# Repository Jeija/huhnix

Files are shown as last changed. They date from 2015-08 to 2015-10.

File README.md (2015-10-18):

# Huhnix
Huhnix is software for an automatic slider door, such as a door for a hen house (hence the name). The slider door opens automatically every morning at a set time and is operated with two buttons or via WiFi. Settings can be adjusted with WiFi device that can access the settings webpage. Huhnix uses two microprocessors that communicate over a UART interface.

## Pictures
Slider with electronics
Configuration site on smartphone
Henhouse with slider and buttons
...and a chicken

## Documentation
### Main controller: AVR
The main processor receives inputs from two buttons that are used to make the doors slide up or down and keeps all the settings and keeps track of the time (so no need for a RTC).

### Secondary controller: ESP8266
The ESP8266 provides a configuration interface by acting as an access point that mobile devices can connect to in order to access a simple web interface. This web interface can be used to access system information such as the system clock and battery levels. The ESP8266 (e.g. within an ESP-01 module) is only active, when the main processor wakes it up. That is the case, when any of the slider control buttons have been pressed. This is crucial to save limited battery power. The battery can be charged using a solar panel. The ESP8266 software is based on the IoT SDK version 1.4 from Espressif.

### Controller communication protocol
#### Definitions
Due to restrictions of the ESP-01 module, the two processors have to communicate over the serial port. The protocol is as follows:
* Baudrate 9600 Baud, no parity, 8 bits, no stopbit, no flow control
* Each processor must always listen for commands and can always send commands. When a processor receives a command, it must answer immediately or perform the requested action and may not execute another command at the same time.
* If any unknown or unexpected string / command / ... is received by any processor, it has to be ignored. This is due to the fact that the ESP8266 SDK ROM outputs debug information, which cannot be disabled.
* Each command is terminated by "\r\n". The command itself may not contain any of these characters.

#### Commands
| ESP8266 command	| Description	|
|---	|---	|
| time	| For debugging only, outputs human-readable DCF77 time information	|
| dcf	| For debugging only, outputs debugging data on the DCF77 signal	|
| time_get	| To be used by the AVR controller. Outputs time data in a machine (and also human) readable form: Seconds, minutes, hours, date (of month), month, year (only last two digits) and day (of week) are transferred in this order as human-readable strings with a space in between each value. If no valid time value is available, the ESP8266 answers with the character x.	|

| AVR command	| Description	|
|---	|---	|
| slider_down	| Move the slider door down. Must be acknowledged by sending the string "sld_ok".	|
| slider_up	| Move the slider door up. Must be acknowledged by sending the string "slu_ok".	|
| systime_get	| Gets the current system time in the same format as time_get (for debugging and for Display on the web frontend).	|
| battery_get	| To be used by the ESP8266. Voltage and percent values are transferred as two human-readable numbers with a space in between them. The voltage value is transferred as an unsigned integer with the value being measured in 100mV (so a value of 123 indicates 12,3V). The percentage value is an estimated integer number between 0 and 100.	|
| opentime_get	| Get time at which to open the slider automatically (time of day). Hours and minutes are transferred as two human-readable integer numbers with a space in between them. An hour value of 25 indicates that the slider is not supposed to be opened at all.	|
| opentime_set <hours> <minutes>	| Tell AVR to open the slider at <hours>:<minutes> each day, where hours and minutes are integers seperate by a space. Must be acknowledged by sending the string "ots_ok"	|

### AVR hardware
The ATMega128A's fusebits are `E:FF, H:89, L:FF`, make sure to disable ATMega 103 compatibility mode! I use a cheap [chinese ATMega128A development board from LC Studio](http://www.lctech-inc.com/Hardware/Detail.aspx?id=68611f14-46cd-4676-95df-f1246689dbba) with the power LED desoldered in order to save power. A custom addon board (PCB design files in `hardware` directory, currently only tested with a prototype board) is stacked on top of the pin headers of the development board. This addon board has connectors for the DCF77 real time clock (I use the one from [conrad.de](http://www.conrad.de/ce/de/product/641138), for buttons, for 12V power sensing, the 5V power supply (provided by a step down converter from a lead-acid battery) and for a 2-channel relay board (HL-52 V 1.0).

## Attribution / License
The PCB design and schematic uses [Jerry Dunmire's ESP8266 KiCAD library](https://github.com/jdunmire/kicad-ESP8266) in the `hardware/libraries/ESP8266` directory, licensed under CC BY-SA 4.0. I license my hardware designs under the [CC BY-SA 4.0 license](https://creativecommons.org/licenses/by-sa/4.0/).

The ESP8266 software uses [Spritetm's libesphttpd with espfs](https://github.com/Spritetm/libesphttpd) in `esp8266/libesphttpd`. All my code is licensed under the [MIT license](http://opensource.org/licenses/MIT).

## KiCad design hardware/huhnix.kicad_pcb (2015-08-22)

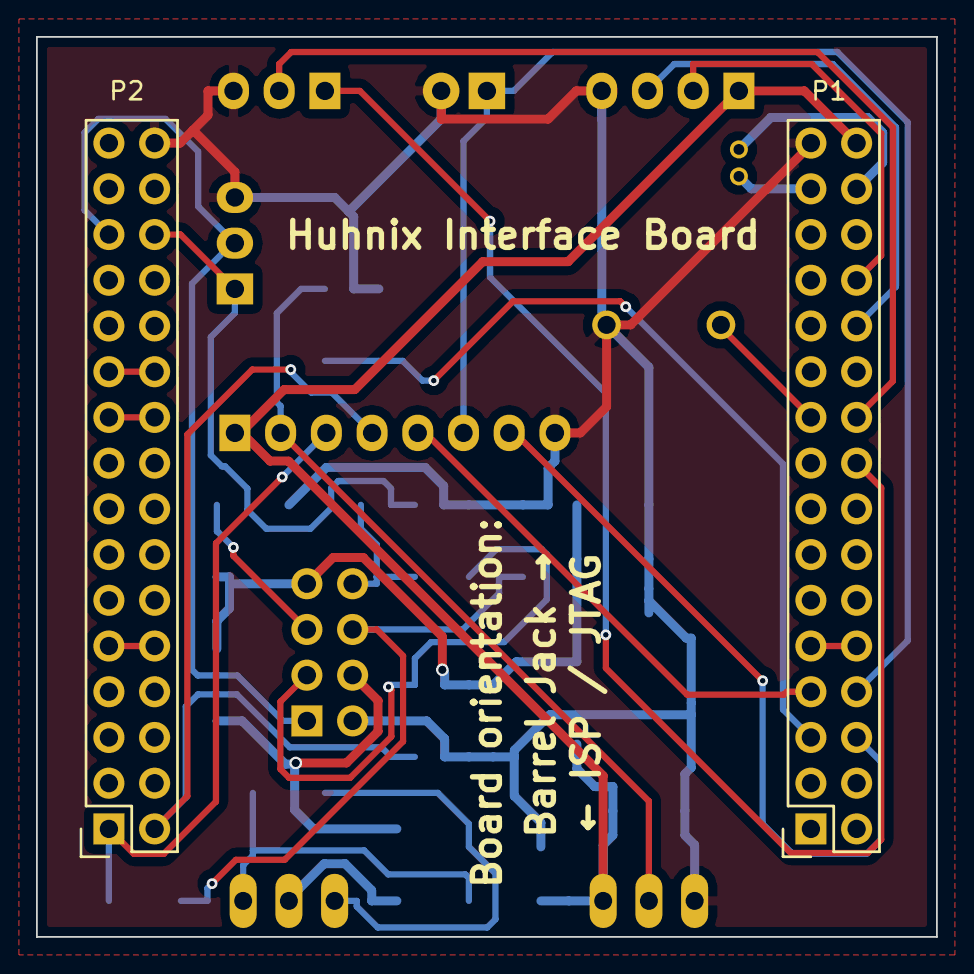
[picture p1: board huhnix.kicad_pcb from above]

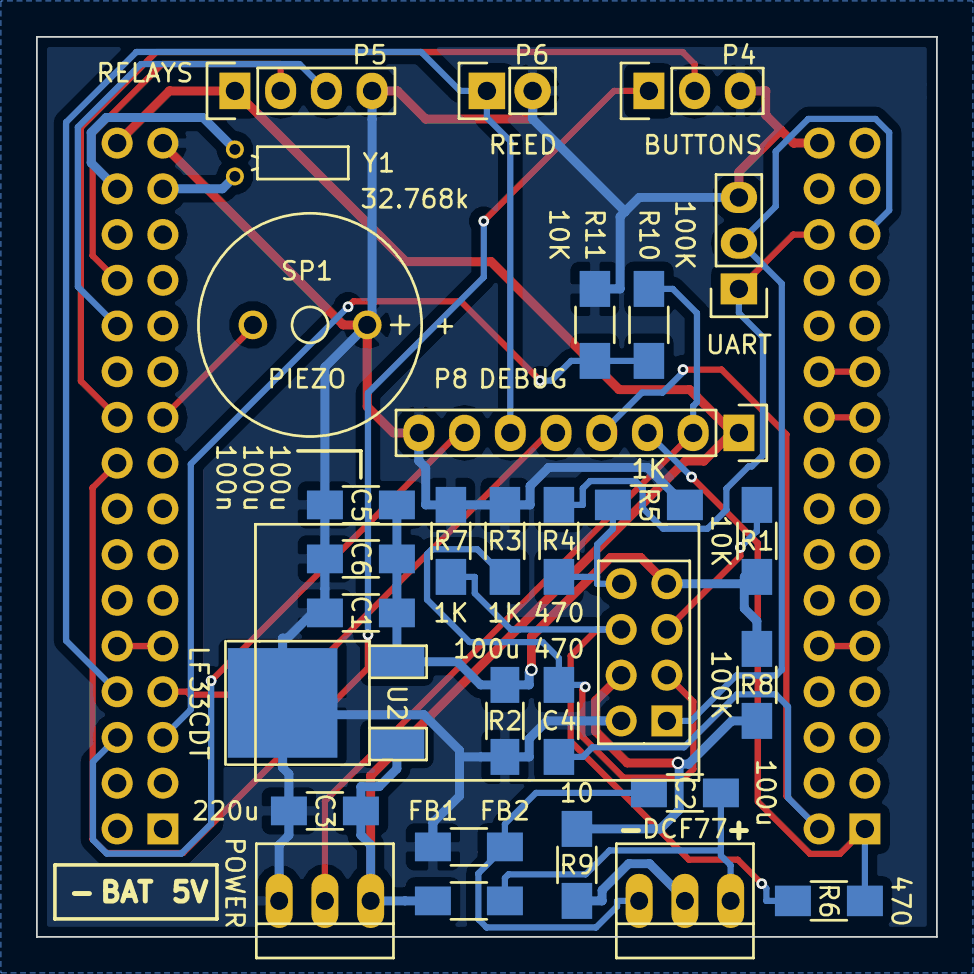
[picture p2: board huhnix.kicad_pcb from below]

Board: 2 copper layers, 50.0 x 50.0 mm, 32 parts (30 on the bottom side), 31 nets.

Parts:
C1: 100n; C_1206_HandSoldering
C2, C4, C5, C6: 100u; C_1206_HandSoldering
C3: 220u; C_1206_HandSoldering
FB1, FB2: FILTER; C_1206_HandSoldering
P1, P2: CONN_02X16; Socket_Strip_Straight_2x16
P3: DCF77; PINHEAD1-3
P4: BUTTONS; Pin_Header_Straight_1x03
P5: RELAYS; Pin_Header_Straight_1x04
P6: REED; Pin_Header_Straight_1x02
P7: POWER; PINHEAD1-3
P8: UART; Pin_Header_Straight_1x03
P9: DEBUG; Pin_Header_Straight_1x08
R1, R11: 10K; R_1206_HandSoldering
R2, R4, R6: 470; R_1206_HandSoldering
R3, R5, R7: 1K; R_1206_HandSoldering
R8, R10: 100K; R_1206_HandSoldering
R9: 10; R_1206_HandSoldering
SP1: PIEZO; MagneticBuzzer_ProSignal_ABT-410-RC
U1: ESP-01v090; ESP-01
U2: LF33CDT; TO-252-2Lead
Y1: 32.768k; Crystal_Round_Horizontal_2mm

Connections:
+3V3: C1.1, C4.1, C5.1, C6.1, R1.1, R8.1, U1.7, U2.3
+5V: C3.1, FB1.1, P1.32, P5.1, P7.1, P9.1, U2.1
+BATT: P7.2, P9.2, R10.1
/Aref: P1.9, P1.10
/PB2: P1.24, P5.3
/PB4: P1.26, P5.2
/PE4: P1.18, P4.1
/PE6: P1.20, P4.2
/PE7: P1.19, SP1.1
/PF0: P1.7, P9.5
/PF1: P1.8, P6.1, P9.6
/PF2: P1.5, R10.2, R11.1
/PF3: P1.6, P9.7
/PG0: P2.21, P2.22
/PG1: P2.19, P2.20
/PG2: P2.9, P2.10
/PG3: P1.30, Y1.1
/PG4: P1.29, Y1.2
DCF: P3.2, R9.2
ESP_EN: P2.2, P9.4, R2.1
ESP_PRGM: P2.1, P9.3, R6.1
GND: C1.2, C3.2, C4.2, C5.2, C6.2, FB2.1, P1.31, P2.32, P4.3, P5.4, P6.2, P7.3, P8.3, P9.8, R3.2, R5.2, R7.2, R11.2, SP1.2, U1.2, U2.2
unnamed: C2.1, FB1.2, P3.1
unnamed: C2.2, FB2.2, P3.3
unnamed: R1.2, U1.5
unnamed: R2.2, R3.1, U1.3
unnamed: R4.2, R5.1, U1.8
unnamed: R6.2, R7.1, U1.6
unnamed: R8.2, R9.1, U1.4
RXD: P2.27, P8.2, U1.1
TXD: P2.28, P8.1, R4.1

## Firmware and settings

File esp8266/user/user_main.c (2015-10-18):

// System
#include "ets_sys.h"
#include "osapi.h"
#include "gpio.h"
#include "os_type.h"
#include "user_interface.h"

// HTTPD
#include "webpages-espfs.h"
#include "httpdespfs.h"
#include "httpd.h"

// Configuration
#include "user_config.h"

bool time_valid = false;
struct TimeSpec {
	uint8_t seconds;
	uint8_t minutes;
	uint8_t hours;
	uint8_t date;
	uint8_t month;
	uint8_t year;
	uint8_t dow;
} time;

bool dcf_decoder_readjust = false;

os_timer_t dcf_read_timer;
os_timer_t dcf_decode_timer;
os_timer_t time_inc_timer;

#define ANS_BUF_SIZE 30
uint8_t ans_buf_iter = 0;
char ans_buf[ANS_BUF_SIZE];

#define CMD_BUF_SIZE 16
uint8_t cmd_buf_iter = 0;
char cmd_buf[CMD_BUF_SIZE];

uint8_t dcf_hc = 0;
uint8_t dcf_lc = 0;

uint8_t signal[60];
uint8_t signal_iter = 0;

#define user_procTaskPrio 0
#define user_procTaskQueueLen 1
os_event_t user_procTaskQueue[user_procTaskQueueLen];

// Returns FALSE if value is invalid
uint8_t decode_value(uint8_t firstbit, uint8_t lastbit) {
	++firstbit; ++lastbit;
	uint8_t bitnum = lastbit - firstbit;
	uint8_t value = 0;

	// No need for math.h's pow() this way
	if (signal[firstbit]) value += 1;
	if (bitnum >= 1 && signal[firstbit + 1]) value += 2;
	if (bitnum >= 2 && signal[firstbit + 2]) value += 4;
	if (bitnum >= 3 && signal[firstbit + 3]) value += 8;

	// BCD notation
	if (bitnum >= 4 && signal[firstbit + 4]) value += 10;
	if (bitnum >= 5 && signal[firstbit + 5]) value += 20;
	if (bitnum >= 6 && signal[firstbit + 6]) value += 40;
	if (bitnum >= 7 && signal[firstbit + 7]) value += 80;

	return value;
}

bool check_parity(uint8_t firstbit, uint8_t lastbit, uint8_t paritybit) {
	++firstbit; ++lastbit; ++paritybit;
	uint8_t i;
	uint8_t parity = 0;
	for (i = firstbit; i <= lastbit; i++)
		parity ^= signal[i];

	return (parity == signal[paritybit]);
}

void dcf2time(void) {
	if (signal_iter == 60) {
		time.seconds = 0;

		// Assume time signal is good only if all parities are correct
		if (check_parity(21, 27, 28) && check_parity(29, 34, 35) && check_parity(36, 57, 58)) {
			time.minutes = decode_value(21, 27);
			time.hours = decode_value(29, 34);
			time.date = decode_value(36, 41);
			time.dow = decode_value(42, 44);
			time.month = decode_value(45, 49);
			time.year = decode_value(50, 57);

			time_valid = true;
		}
	}
}

/*** Timers ***/
void dcf_decode_timer_cb(void) {
	// Last second of minute, no time signal, readjust
	if (dcf_hc <= 10) {
		dcf2time();
		signal_iter = 0;
		os_timer_disarm(&dcf_decode_timer);
		dcf_decoder_readjust = true;
	}

	if (signal_iter < 60) signal[signal_iter++] = (dcf_hc > 35);
	dcf_lc = 0;
	dcf_hc = 0;
}

void dcf_decode_timer_adjust(void) {
	os_timer_disarm(&dcf_decode_timer);
	os_timer_setfn(&dcf_decode_timer, (os_timer_func_t *) dcf_decode_timer_cb, NULL);
	os_timer_arm(&dcf_decode_timer, 1000, 1);
}

void dcf_read_timer_cb(void)
{
	// Inverted signal, add to low count (lc) when pin is true
	if (GPIO_INPUT_GET(2)) {
		dcf_lc++;
		if (dcf_decoder_readjust) {
			dcf_decode_timer_adjust();
			dcf_decoder_readjust = false;
		}
	} else
		dcf_hc++;
}

void time_inc_timer_cb(void) {
	time.seconds++;
	if (time.seconds == 60) {
		time.seconds = 0;
		time.minutes++;
		if (time.minutes == 60) {
			time.minutes = 0;
			time.hours++;
			if (time.hours == 24) {
				time.hours = 0;
				time.date++;
				time.dow++;
				// Ignore the rest, receive that from DCF77
			}
		}
	}
}

void ap_init(void) {
	// Check if configuration is ok already (compare SSID)
	struct softap_config netcfg;

	wifi_softap_get_config(&netcfg);
	if (os_strcmp(WIFI_SSID, netcfg.ssid) == 0) return;

	// Configuration is not good, change config and reboot
	system_restore();
	os_memcpy(netcfg.ssid, WIFI_SSID, os_strlen(WIFI_SSID));
	netcfg.ssid[os_strlen(WIFI_SSID)] = 0x00;
	netcfg.ssid_len = os_strlen(WIFI_SSID);
	netcfg.channel = 1;
	netcfg.authmode = AUTH_OPEN;
	netcfg.beacon_interval = 100;

	wifi_softap_set_config(&netcfg);
	wifi_set_opmode(0x02);
	system_restart();
}

/*** Loop ***/
static void ICACHE_FLASH_ATTR loop(os_event_t *events) {
	char c;
	int res = uart_rx_one_char(&c);

	if(res != 1) {
		if (c != '\r' && c != '\n') {
			if (cmd_buf_iter + 1 < CMD_BUF_SIZE)
				cmd_buf[cmd_buf_iter++] = c;
		} else {
			cmd_buf[cmd_buf_iter] = 0x00;
			cmd_buf_iter = 0;
			if (os_strcmp(cmd_buf, "time") == 0) {
				if (time_valid) {
					os_printf("Zeit: %d.%d.%d, %d:%d:%d, DOW %d\r\n", time.date, time.month, time.year, time.hours, time.minutes, time.seconds, time.dow);
				} else {
					os_printf("No valid time information yet!\r\n");
				}
			} else if (os_strcmp(cmd_buf, "dcf") == 0) {
				os_printf("DCF77 status information:\r\n");
				os_printf("Received bits this minute: %d\r\n", signal_iter);
				os_printf("High count %d, Low count %d, Total %d\r\n", dcf_hc, dcf_lc, dcf_hc + dcf_lc);
				os_printf("Signal buffer:\r\n");
				uint8_t i;
				for (i = 0; i < 60; i++) os_printf("%d", signal[i]);
				os_printf("\r\n");
			} else if (os_strcmp(cmd_buf, "time_get") == 0) {
				if (time_valid) {
					os_printf("%d %d %d %d %d %d %d\r\n", time.seconds, time.minutes, time.hours, time.date, time.month, time.year, time.dow);
				} else {
					os_printf("x\r\n");
				}
			} else if (os_strcmp(cmd_buf, "hello") == 0) {
				os_printf("hel_ok\r\n");
			}
		}
	}
	system_os_post(user_procTaskPrio, 0, 0);
}

/**
 * get_answer
 * Writes answer in global ans_buf variable
 * Ignores answers that are longer than ANS_BUF_SIZE
 * Returns false if no answer was received, otherwise true
 *
 * ms_to_answer maximum 1000ms due to watchdog!
 */
bool get_answer(uint16_t ms_to_answer) {
	ans_buf_iter = 0;
	uint16_t time_ms = 0;

	while (time_ms <= ms_to_answer) {
		char c;
		int res = uart_rx_one_char(&c);

		if (res == 1) {
			os_delay_us(1000);
			time_ms++;
		} else {
			if (c != '\r' && c != '\n') {
				if (ans_buf_iter + 1 < ANS_BUF_SIZE)
					ans_buf[ans_buf_iter++] = c;
			} else {
				ans_buf[ans_buf_iter] = 0x00;
				return true;
			}
		}
	}

	return false;
}

/**
 * Returns the nth integer from a string in which integers are separated by spaces
 * The integer must be an unsigned 8-bit integer, the string must be null-terminated
 * Returns 255 on error (nth too high), but string must contain valid integers
 */
uint8_t integer_from_string(char *buf, uint8_t nth) {
	char numberbuf[4];
	uint8_t numberbuf_iter = 0;
	uint8_t i = 0;
	uint8_t intnum = 0;
	while (buf[i] != 0x00) {
		if (buf[i] == ' ') {
			intnum++;
			if (intnum > nth) break;
		} else if (intnum == nth) {
			numberbuf[numberbuf_iter++] = buf[i];
		}

		i++;
	}

	if (intnum < nth) return 255;

	numberbuf[numberbuf_iter] = 0x00;
	return (uint8_t) atoi(numberbuf);
}

/**
 * HTTP commands
 * They forward the corresponding command to the AVR controller and decode the
 * answer. The may then forward that answer to the HTTP client in a human-readable
 * format.
 */
int cmd_slider_up(HttpdConnData *conn) {
	uint8_t i;
	for (i = 0; i < 4; i++) {
		os_printf("\r\nslider_up\r\n");
		bool res = get_answer(200);
		if (res == true && os_strcmp("slu_ok", ans_buf) == 0) {
			os_printf("Leaving with success state\r\n");
			httpdSend(conn, "ok", -1);
			return HTTPD_CGI_DONE;
		}
	}

	os_printf("Leaving with error state, buffer is %s\r\n", ans_buf);
	httpdSend(conn, "Keine Antwort vom AVR-Controller", -1);
	return HTTPD_CGI_DONE;
}

int cmd_slider_down(HttpdConnData *conn) {
	uint8_t i;
	for (i = 0; i < 4; i++) {
		os_printf("\r\nslider_down\r\n");
		bool res = get_answer(200);
		if (res == true && os_strcmp("sld_ok", ans_buf) == 0) {
			httpdSend(conn, "ok", -1);
			return HTTPD_CGI_DONE;
		}
	}

	httpdSend(conn, "Keine Antwort vom AVR-Controller", -1);
	return HTTPD_CGI_DONE;
}

int cmd_opentime_get(HttpdConnData *conn) {
	uint8_t i;
	for (i = 0; i < 4; i++) {
		os_printf("\r\nopentime_get\r\n");
		bool res = get_answer(200);
		if (res == true) {
			uint8_t hours = integer_from_string(ans_buf, 0);
			uint8_t minutes = integer_from_string(ans_buf, 1);

			char resbuf[50];
			if (hours == 25)
				os_sprintf(resbuf, "Klappe wird nicht automatisch geöffnet");
			else
				os_sprintf(resbuf, "Aufmachzeit ist %d:%d Uhr", hours, minutes);
			httpdSend(conn, resbuf, -1);
			return HTTPD_CGI_DONE;
		}
	}

	httpdSend(conn, "Keine Antwort vom AVR-Controller", -1);
	return HTTPD_CGI_DONE;
}

int cmd_systime_get(HttpdConnData *conn) {
	uint8_t i;
	for (i = 0; i < 4; i++) {
		os_printf("\r\nsystime_get\r\n");
		bool res = get_answer(200);
		if (res == true) {
			uint8_t seconds = integer_from_string(ans_buf, 0);
			uint8_t minutes = integer_from_string(ans_buf, 1);
			uint8_t hours = integer_from_string(ans_buf, 2);
			uint8_t date = integer_from_string(ans_buf, 3);
			uint8_t month = integer_from_string(ans_buf, 4);
			uint8_t year = integer_from_string(ans_buf, 5);
			uint8_t dow = integer_from_string(ans_buf, 6);

			char dow_readable[30];
			if (dow == 255) continue;
			else if (dow == 1) os_strcpy(dow_readable, "Montag");
			else if (dow == 2) os_strcpy(dow_readable, "Dienstag");
			else if (dow == 3) os_strcpy(dow_readable, "Mittwoch");
			else if (dow == 4) os_strcpy(dow_readable, "Donnerstag");
			else if (dow == 5) os_strcpy(dow_readable, "Freitag");
			else if (dow == 6) os_strcpy(dow_readable, "Samstag");
			else if (dow == 7) os_strcpy(dow_readable, "Sonntag");
			else if (dow == 0) os_strcpy(dow_readable, "Ungültige Systemzeit");

			char resbuf[80];
			os_sprintf(resbuf, "%s, %d.%d.%d %d:%d:%d Uhr", dow_readable, date, month, year, hours, minutes, seconds);
			httpdSend(conn, resbuf, -1);
			return HTTPD_CGI_DONE;
		}
	}

	httpdSend(conn, "Keine Antwort vom AVR-Controller", -1);
	return HTTPD_CGI_DONE;
}

int cmd_systime_set(HttpdConnData *conn) {
	// Parse command from GET parameters
	char seconds_str[3];
	char minutes_str[3];
	char hours_str[3];
	char date_str[3];
	char month_str[3];
	char year_str[3];
	char dow_str[2];

	httpdFindArg(conn->getArgs, "seconds", seconds_str, sizeof(seconds_str));
	httpdFindArg(conn->getArgs, "minutes", minutes_str, sizeof(minutes_str));
	httpdFindArg(conn->getArgs, "hours", hours_str, sizeof(hours_str));
	httpdFindArg(conn->getArgs, "date", date_str, sizeof(date_str));
	httpdFindArg(conn->getArgs, "month", month_str, sizeof(month_str));
	httpdFindArg(conn->getArgs, "year", year_str, sizeof(year_str));
	httpdFindArg(conn->getArgs, "dow", dow_str, sizeof(dow_str));

	time.seconds = atoi(seconds_str);
	time.minutes = atoi(minutes_str);
	time.hours = atoi(hours_str);
	time.date = atoi(date_str);
	time.month = atoi(month_str);
	time.year = atoi(year_str);
	time.dow = atoi(dow_str);
	time_valid = true;

	httpdSend(conn, "ok", -1);
	return HTTPD_CGI_DONE;
}

int cmd_battery_get(HttpdConnData *conn) {
	uint8_t i;
	for (i = 0; i < 4; i++) {
		os_printf("\r\nbattery_get\r\n");
		bool res = get_answer(200);
		if (res == true) {
			uint8_t voltage = integer_from_string(ans_buf, 0);
			uint8_t percent = integer_from_string(ans_buf, 1);

			char resbuf[50];
			os_sprintf(resbuf, "Batteriespannung ist %u.%uV, geschätzt %u%", (voltage - voltage % 10) / 10, voltage % 10, percent);
			httpdSend(conn, resbuf, -1);
			return HTTPD_CGI_DONE;
		}
	}

	httpdSend(conn, "Keine Antwort vom AVR-Controller", -1);
	return HTTPD_CGI_DONE;
}

int cmd_opentime_set(HttpdConnData *conn) {
	// Parse command from GET parameters
	char hours_str[5];
	char minutes_str[5];

	httpdFindArg(conn->getArgs, "hours", hours_str, sizeof(hours_str));
	httpdFindArg(conn->getArgs, "minutes", minutes_str, sizeof(minutes_str));

	char command[30];
	os_sprintf(command, "\r\nopentime_set %s %s\r\n", hours_str, minutes_str);

	// Send command / wait for answer
	uint8_t i;
	for (i = 0; i < 4; i++) {
		os_printf(command);
		bool res = get_answer(200);
		if (res == true && os_strcmp("ots_ok", ans_buf) == 0) {
			httpdSend(conn, "ok", -1);
			return HTTPD_CGI_DONE;
		}
	}

	httpdSend(conn, "Keine Antwort vom AVR-Controller", -1);
	return HTTPD_CGI_DONE;
}

int cmd_dcf_info(HttpdConnData *conn) {
	char buf[500];
	os_sprintf(buf, "DCF77 status information:\r\nReceived bits this minute: %d\r\nHigh count %d, Low count %d, Total %d\r\nSignal buffer:\r\n", signal_iter, dcf_hc, dcf_lc, dcf_hc + dcf_lc);

	uint16_t begin = 0;
	uint8_t i;
	while (buf[++begin]);
	for (i = 0; i < 60; ++i) buf[begin + i] = signal[i] ? '1' : '0';
	buf[begin + i] = 0x00;

	httpdSend(conn, buf, -1);
	return HTTPD_CGI_DONE;
}

HttpdBuiltInUrl builtInUrls[] = {
	{"/", cgiRedirect, "/index.html"},
	{"/slider_up", cmd_slider_up, NULL},
	{"/slider_down", cmd_slider_down, NULL},
	{"/opentime_get", cmd_opentime_get, NULL},
	{"/systime_get", cmd_systime_get, NULL},
	{"/systime_set", cmd_systime_set, NULL},
	{"/battery_get", cmd_battery_get, NULL},
	{"/opentime_set", cmd_opentime_set, NULL},
	{"/dcf_info", cmd_dcf_info, NULL},
	{"*", cgiEspFsHook, NULL},
	{NULL, NULL, NULL}
};

/*** Main function ***/
void ICACHE_FLASH_ATTR user_init() {
	uart_div_modify(0, UART_CLK_FREQ / BAUD);
	os_printf("Startup from %d...\r\n", system_get_rst_info()->reason);
	gpio_init();
	ap_init();

	// HTTPD
	espFsInit((void*)(webpages_espfs_start));
	httpdInit(builtInUrls, 80);

	// Set GPIO2 (DCF77 pin) to input, disable pullup
	gpio_output_set(0, 0, 0, 2);
	PIN_PULLUP_DIS(PERIPHS_IO_MUX_GPIO2_U);

	// DCF77 read timer
	os_timer_disarm(&dcf_read_timer);
	os_timer_setfn(&dcf_read_timer, (os_timer_func_t *) dcf_read_timer_cb, NULL);
	os_timer_arm(&dcf_read_timer, 5, 1);

	// Second increase timer
	os_timer_disarm(&time_inc_timer);
	os_timer_setfn(&time_inc_timer, (os_timer_func_t *) time_inc_timer_cb, NULL);
	os_timer_arm(&time_inc_timer, 1000, 1);

	// DCF77 decode timer: decide wheter 1 or 0
	dcf_decode_timer_adjust();

	os_printf(" completed!\r\n\r\n");
	system_os_task(loop, user_procTaskPrio, user_procTaskQueue, user_procTaskQueueLen);
	system_os_post(user_procTaskPrio, 0, 0);
}

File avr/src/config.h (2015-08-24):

// UART1 configuration
#define BAUD 9600

// Buffer configurations, internals, ...
#define CMD_BUF_SIZE 40

// EEPROM layout
#define EEPROM_OFFSET 0x00

/*** Hardware connections ***/
// Buttons
#define BUTTON_PORT PORTE
#define BUTTON_DDR DDRE
#define BUTTON_PIN PINE
#define BUTTON1_BIT PE4
#define BUTTON2_BIT PE6
#define BUTTON_EICR EICRB
#define BUTTON1_ISC 0x00
#define BUTTON2_ISC 0x00
#define BUTTON1_INT (1<<INT4)
#define BUTTON2_INT (1<<INT6)
#define BUTTON1_vect INT4_vect
#define BUTTON2_vect INT6_vect

// Slider reed contact
#define REED_PORT PORTF
#define REED_DDR DDRF
#define REED_PIN PINF
#define REED_BIT PF1

// Slider motors (to relays)
#define RELAY_PORT PORTB
#define RELAY_DDR DDRB
#define RELAY1_BIT PB2
#define RELAY2_BIT PB4

// Piezo loudspeaker
#define PIEZO_PORT PORTE
#define PIEZO_DDR DDRE
#define PIEZO_BIT PE7

// Battery, factor depends on voltage devider specifics
#define BATT_ADC 2
#define BATT_MIN 115
#define BATT_MAX 130
#define BATT_ADC_FACTOR 116

// ESP8266
#define ESP_PORT PORTA
#define ESP_DDR DDRA
#define ESP_ENABLE PA0
#define ESP_PROGRAM PA1

// Input value counts
#define INPUT_VALID_COUNT 1000
#define SLIDER_UP_EMERGENCY_STOP_COUNT 1200000

// Timing
#define SLIDER_DOWN_TIME 6
#define SLIDER_UP_TIME_MAX 25
#define TIME_UPDATE_INTERVAL 10
#define TIME_UPDATE_MAXAGE 20
#define TIME_UPDATE_WARN_AGE ((uint64_t)3600 * 24 * 7)
#define MAX_WAKE_TIME (60 * 6)

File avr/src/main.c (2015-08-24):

// System
#include <avr/interrupt.h>
#include <util/delay.h>
#include <avr/sleep.h>
#include <stdbool.h>
#include <avr/io.h>
#include <string.h>
#include <stdlib.h>

// Project
#include "config.h"
#include "uart.h"
#include "util.h"
#include "main.h"

// true = up, false = down
SliderPos slider_state = SLIDER_DOWN;
SliderPos slider_wanted = SLIDER_UP;

// Command answer buffer
#define ANS_BUF_SIZE 30
char ans_buf[ANS_BUF_SIZE] = {0x00};

// Timing
#define BEGIN_TIMESTAMP 0
bool time_correct = false;
struct TimeSpec time;
uint64_t timestamp = BEGIN_TIMESTAMP;
uint64_t last_timesync_timestamp = BEGIN_TIMESTAMP;
uint64_t wakeup_timestamp = BEGIN_TIMESTAMP;

uint64_t slider_down_begin_timestamp = BEGIN_TIMESTAMP;
uint64_t slider_up_begin_timestamp = BEGIN_TIMESTAMP;

// Action flags
bool action_updtime = false;
bool wakeup_slider = false;
bool wakeup_button = false;
bool force_sleep = false;
bool action_espreset = false;

// Reed counts
uint16_t button1_count = 0;
uint16_t button2_count = 0;
uint16_t reed_count = 0;

/**
 * get_answer()
 * Writes answer in global ans_buf variable
 * Ignores answers that are longer than ANS_BUF_SIZE
 * Returns false if no answer was received, otherwise true
 */
bool get_answer(uint16_t ms_to_answer) {
	uint8_t ans_buf_iter = 0;
	uint16_t time_ms = 0;

	while (time_ms <= ms_to_answer) {
		char c;
		if (uart_getc(&c)) {
			if (c != '\r' && c != '\n') {
				if (ans_buf_iter + 1 < ANS_BUF_SIZE)
					ans_buf[ans_buf_iter++] = c;
			} else {
				ans_buf[ans_buf_iter] = 0x00;
				return true;
			}
		} else {
			_delay_ms(1);
			time_ms++;
		}
	}

	return false;
}

/**
 * init()
 * Setup ports for input and output
 */
void init() {
	// ESP8266 pins
	sbi(ESP_DDR, ESP_ENABLE);
	sbi(ESP_DDR, ESP_PROGRAM);

	// Reed contact and buttons are connected to GND, so use internal pullups
	sbi(BUTTON_PORT, BUTTON1_BIT);
	sbi(BUTTON_PORT, BUTTON2_BIT);
	sbi(REED_PORT, REED_BIT);

	// Piezo
	sbi(PIEZO_DDR, PIEZO_BIT);

	// Motor relays; on = GND, off = 5v
	// RELAY1 = off, RELAY2 = off: No movement
	// RELAY1 = on, RELAY2 = off: Up
	// RELAY1 = off, RELAY2 = on: Down
	// RELAY1 = on, RELAY2 = on: No movement
	sbi(RELAY_DDR, RELAY1_BIT);
	sbi(RELAY_DDR, RELAY2_BIT);
	sbi(RELAY_PORT, RELAY1_BIT);
	sbi(RELAY_PORT, RELAY2_BIT);

	// Wait for RTC oscillator to stabilize
	_delay_ms(200);

	// RTC oscillator (at the very end, so crystal is more stable)
	// See AVR application note 134 for more information
	TIMSK &= ~((1<<TOIE0) | (1<<OCIE0));
	ASSR |= (1<<AS0);
	TCNT0 = 0;
	TCCR0 = (1<<CS00) | (1<<CS02);
	while(ASSR & ((1<<TCN0UB) | (1<<OCR0UB) || (1<<TCR0UB)));
	TIMSK |= (1<<TOIE0);

	// PF4 - PF7 high to reduce power consumption caused by pullups on the dev board
	sbi(DDRF, 4);
	sbi(DDRF, 5);
	sbi(DDRF, 6);
	sbi(DDRF, 7);
	sbi(PORTF, 4);
	sbi(PORTF, 5);
	sbi(PORTF, 6);
	sbi(PORTF, 7);
}

void esp_startup() {
	/* Start ESP8266 */
	// everything off
	cbi(ESP_PORT, ESP_ENABLE);
	cbi(ESP_PORT, ESP_PROGRAM);
	_delay_ms(500);
	// normal operation
	sbi(ESP_PORT, ESP_PROGRAM);
	_delay_ms(300);
	// startup
	sbi(ESP_PORT, ESP_ENABLE);
	_delay_ms(700);

	uart_flush();
}

/**
 * The step-down converter does not provide consistent current supply when a
 * lot of current is drawn. Therefore, the ESP8266 will only be enabled when
 * the motor / the relays are not active. Since there is no reliable DCF signal
 * and no good WiFi signal transmission while the motors are active, this makes sense.
 */
void esp_disable() {
	cbi(ESP_PORT, ESP_PROGRAM);
	cbi(ESP_PORT, ESP_ENABLE);
}

// Starts up ESP8266 multiple times until the ESP responds, or fails with error beep code
void esp_start_test() {
	// Check if ESP8266 is ok
	// Multiple attempts to start the ESP8266 may be required, since the
	uint8_t tries;
	bool success = false;
	for (tries = 0; tries < 12; ++tries) {
		uart_puts("hello\r\n");
		if (tries != 0 && tries % 2 == 0) esp_startup();
		if (get_answer(100) && strcmp(ans_buf, "hel_ok") == 0) {
			success = true;
			break;
		}
	}

	// ESP8266 not responding, error code deep - long high - deep
	if (!success) {
		uint8_t i;
		for (i = 0; i < 4; i++) {
			sound(7, 300);
			sound(2, 1000);
			sound(7, 300);
			_delay_ms(400);
		}
	}
}

void slider_up() {
	if (slider_wanted != SLIDER_UP) {
		slider_up_begin_timestamp = timestamp;
		esp_disable();
	}
	slider_wanted = SLIDER_UP;
}

void slider_down() {
	if (slider_wanted != SLIDER_DOWN) {
		slider_down_begin_timestamp = timestamp;
		esp_disable();
	}
	slider_wanted = SLIDER_DOWN;
}

/**
 * startup()
 * To be executed after initial startup or after wakeup
 */
void startup() {
	sound(4, 100);

	/** System check / Error reporting **/
	// Twice, WiFi sometimes doesn't work on first startup
	if (slider_state == slider_wanted) {
		esp_startup();
		action_espreset = true;
	}

	// Time has not been synced for a week - warning (long deep - triple high)
	if (timestamp - last_timesync_timestamp > TIME_UPDATE_WARN_AGE || !time_correct) {
		uint8_t i;
		for (i = 0; i < 4; i++) {
			sound(3, 50);
			sound(2, 50);
			sound(1, 50);
			sound(15, 600);
		}
	}

	// Low battery warning (triple high, slow)
	if (battery_voltage_get() <= 120) {
		uint8_t i;
		for (i = 0; i < 4; i++) {
			sound(1, 300);
			_delay_ms(100);
			sound(1, 300);
			_delay_ms(100);
			sound(1, 300);
			_delay_ms(300);
		}
	}

	// Play startup sound
	uart_puts("Huhnix started!\r\n");
	sound(3, 100);
	_delay_ms(30);
	sound(3, 100);
}


/**
 * handle_command()
 * Parse command and execute it, called by handle_shell
 */
void handle_command(char *command, char *args) {
	if (!strcmp(command, "opentime_set")) {
		uint8_t hours = integer_from_string(args, 0);
		uint8_t minutes = integer_from_string(args, 1);
		if (hours <= 25 && minutes < 60) {
			opentime_set(hours, minutes);
			uart_puts("ots_ok\r\n");
		}
	} else if (!strcmp(command, "opentime_get")) {
		uint8_t hours;
		uint8_t minutes;
		opentime_get(&hours, &minutes);
		uart_puti(hours, 10);
		uart_putc(' ');
		uart_puti(minutes, 10);
		uart_puts("\r\n");
	} else if (!strcmp(command, "slider_up")) {
		slider_up();
		uart_puts("slu_ok\r\n");
	} else if (!strcmp(command, "slider_down")) {
		slider_down();
		uart_puts("sld_ok\r\n");
	} else if (!strcmp(command, "systime_get")) {
		uart_puti(time.seconds, 10);
		uart_putc(' ');
		uart_puti(time.minutes, 10);
		uart_putc(' ');
		uart_puti(time.hours, 10);
		uart_putc(' ');
		uart_puti(time.date, 10);
		uart_putc(' ');
		uart_puti(time.month, 10);
		uart_putc(' ');
		uart_puti(time.year, 10);
		uart_putc(' ');
		uart_puti(time_correct ? time.dow : 0, 10);
		uart_puts("\r\n");
	} else if (!strcmp(command, "battery_get")) {
		// Simple linear interpolation for calculating the percentage value
		uint8_t voltage = battery_voltage_get();
		uint8_t percent = 100 * (voltage - BATT_MIN) / (BATT_MAX - BATT_MIN);
		uart_puti(voltage, 10);
		uart_putc(' ');
		uart_puti(percent, 10);
		uart_puts("\r\n");
	}
}
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

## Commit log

2015-08-22 Initial upload
    [huhnix.kicad_pcb, huhnix.sch]
2015-08-24 Fix integer length of TIME_UPDATE_WARN_AGE from 16-bit to 64-bit
    The 16-bit integer caused time-not-synchronized warnings at startup even
    though the AVR had perfectly good, recent time information.
    Some minor cleanups.
    [config.h, main.c]
